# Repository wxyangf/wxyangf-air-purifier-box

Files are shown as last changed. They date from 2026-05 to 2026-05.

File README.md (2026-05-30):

Corsi-Rosenthol Inspired Air Purifier

Onshape Available Here: https://cad.onshape.com/documents/9fe4c8aaf9f949d23d7b46f2/w/0d3218e59a3f068a2d390f4a/e/8d3bb73142d813d5a04eb98a (This Is Based on the version tagged "Public Release")

The concept was to have a Corsi-Rosenthol like design, but a bit more refined.

The big problem that I aimed to address with this design is the difficulty of changing the filters in a regular Corsi-Rosenthol air purifier.

no flow rate tests, because it will heavily depend on the fans you decide to use.

TODO:

* write a proper bom
* add assembly instructions
* update the clip design to not self loosen if turned CCW
* add design for decorative side panels

images:

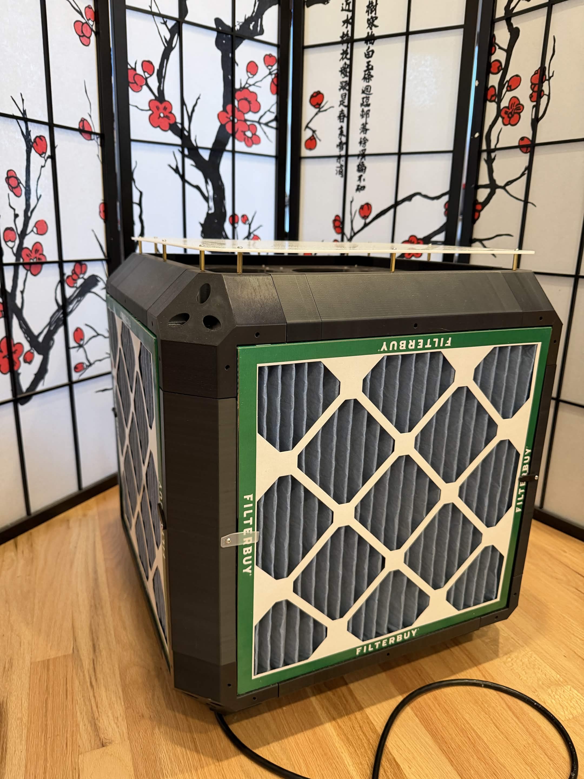
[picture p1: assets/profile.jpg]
image of air purifier in side profile

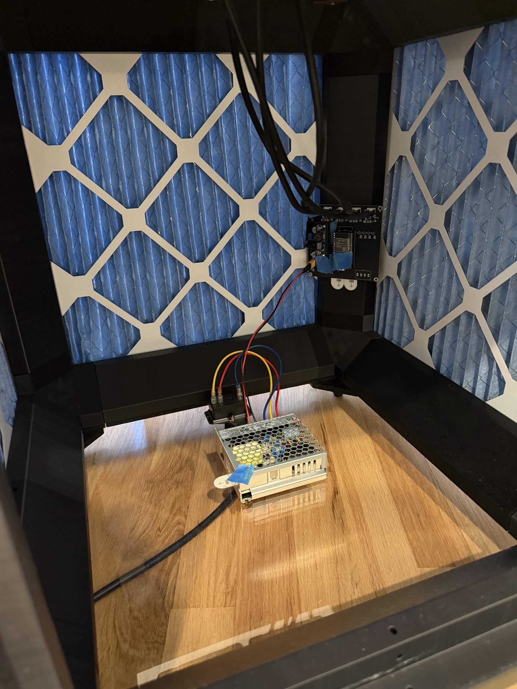
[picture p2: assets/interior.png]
image of the interior of the air purifier

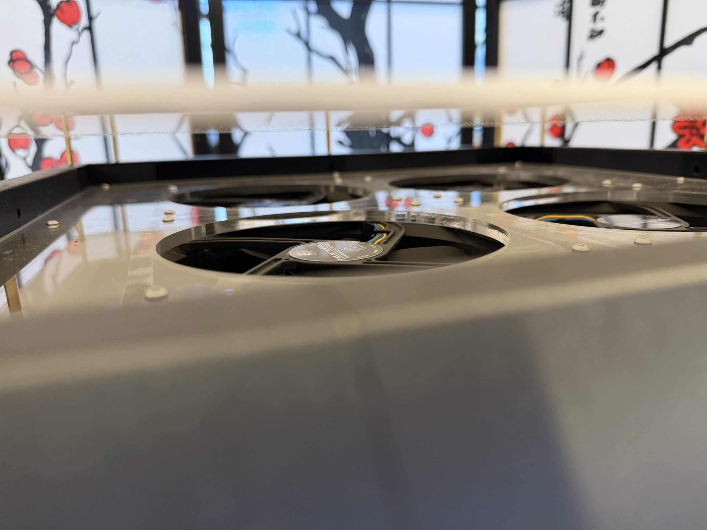
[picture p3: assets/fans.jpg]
image of the fans from the top, under the hat


Notes:

I was too lazy to design my own so voltage regulator part used: https://www.amazon.com/dp/B07VVXF7YX

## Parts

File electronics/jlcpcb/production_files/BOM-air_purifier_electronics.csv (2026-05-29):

Comment | Designator | Footprint | LCSC | Quantity
1.5k | R22 | R_0805_2012Metric_Pad1.20x1.40mm_HandSolder | C4310 | 1
100k | R10,R14,R3,R6 | R_0805_2012Metric_Pad1.20x1.40mm_HandSolder | C22356675 | 4
4.7k | R17,R18,R19,R20,R23 | R_0805_2012Metric_Pad1.20x1.40mm_HandSolder | C22356680 | 5
680 | R21 | R_0805_2012Metric_Pad1.20x1.40mm_HandSolder | C17798 | 1
BSS138 | Q1,Q2,Q3,Q4 | SOT-23 | C52895 | 4
Fan_4pin | M1,M2,M3,M4 | FanPinHeader_1x04_P2.54mm_Vertical | C19795120 | 4
LED | D1,D2,D3 | LED_0805_2012Metric_Pad1.15x1.40mm_HandSolder | C2296 | 3
TPS22810DBV | U3,U4,U5,U6 | SOT-23-6 | C205990 | 4
Conn_01x04_Socket | J2 | TerminalBlock_Altech_AK300-4_P5.00mm |  | 1
TestPoint_Probe | TP7 | TestPoint_THTPad_2.0x2.0mm_Drill1.0mm |  | 1
TestPoint_Probe | TP16 | TestPoint_THTPad_2.0x2.0mm_Drill1.0mm |  | 1
Conn_01x02_Socket | J1 | AMASS_XT30U-M_1x02_P5.0mm_Vertical |  | 1
TestPoint_Probe | TP14 | TestPoint_THTPad_2.0x2.0mm_Drill1.0mm |  | 1
TestPoint_Probe | TP18 | TestPoint_THTPad_2.0x2.0mm_Drill1.0mm |  | 1
TestPoint_Probe | TP3 | TestPoint_THTPad_2.0x2.0mm_Drill1.0mm |  | 1
TestPoint_Probe | TP17 | TestPoint_THTPad_2.0x2.0mm_Drill1.0mm |  | 1
TestPoint_Probe | TP9 | TestPoint_THTPad_2.0x2.0mm_Drill1.0mm |  | 1
TestPoint_Probe | TP15 | TestPoint_THTPad_2.0x2.0mm_Drill1.0mm |  | 1
TestPoint_Probe | TP4 | TestPoint_THTPad_2.0x2.0mm_Drill1.0mm |  | 1
TestPoint_Probe | TP10 | TestPoint_THTPad_2.0x2.0mm_Drill1.0mm |  | 1
TestPoint_Probe | TP11 | TestPoint_THTPad_2.0x2.0mm_Drill1.0mm |  | 1
TestPoint_Probe | TP13 | TestPoint_THTPad_2.0x2.0mm_Drill1.0mm |  | 1
1uF | C3 | C_0805_2012Metric_Pad1.18x1.45mm_HandSolder |  | 1
TestPoint_Probe | TP20 | TestPoint_THTPad_2.0x2.0mm_Drill1.0mm |  | 1
1uF | C2 | C_0805_2012Metric_Pad1.18x1.45mm_HandSolder |  | 1
1uF | C4 | C_0805_2012Metric_Pad1.18x1.45mm_HandSolder |  | 1
TestPoint_Probe | TP5 | TestPoint_THTPad_2.0x2.0mm_Drill1.0mm |  | 1
~ | U2 | buck_boost_module |  | 1
TestPoint_Probe | TP21 | TestPoint_THTPad_2.0x2.0mm_Drill1.0mm |  | 1
TestPoint_Probe | TP2 | TestPoint_THTPad_2.0x2.0mm_Drill1.0mm |  | 1
TestPoint_Probe | TP8 | TestPoint_THTPad_2.0x2.0mm_Drill1.0mm |  | 1
1uF | C1 | C_0805_2012Metric_Pad1.18x1.45mm_HandSolder |  | 1
TestPoint_Probe | TP19 | TestPoint_THTPad_2.0x2.0mm_Drill1.0mm |  | 1
TestPoint_Probe | TP12 | TestPoint_THTPad_2.0x2.0mm_Drill1.0mm |  | 1
TestPoint_Probe | TP6 | TestPoint_THTPad_2.0x2.0mm_Drill1.0mm |  | 1
ESP32-DevKitC | U1 | nodemcu-32s |  | 1
1uF | C9 | C_0805_2012Metric_Pad1.18x1.45mm_HandSolder |  | 1
100nF | C5 | C_0805_2012Metric_Pad1.18x1.45mm_HandSolder |  | 1
100nF | C6 | C_0805_2012Metric_Pad1.18x1.45mm_HandSolder |  | 1
1uF | C10 | C_0805_2012Metric_Pad1.18x1.45mm_HandSolder |  | 1
100nF | C8 | C_0805_2012Metric_Pad1.18x1.45mm_HandSolder |  | 1
100nF | C7 | C_0805_2012Metric_Pad1.18x1.45mm_HandSolder |  | 1
1uF | C11 | C_0805_2012Metric_Pad1.18x1.45mm_HandSolder |  | 1
1uF | C12 | C_0805_2012Metric_Pad1.18x1.45mm_HandSolder |  | 1

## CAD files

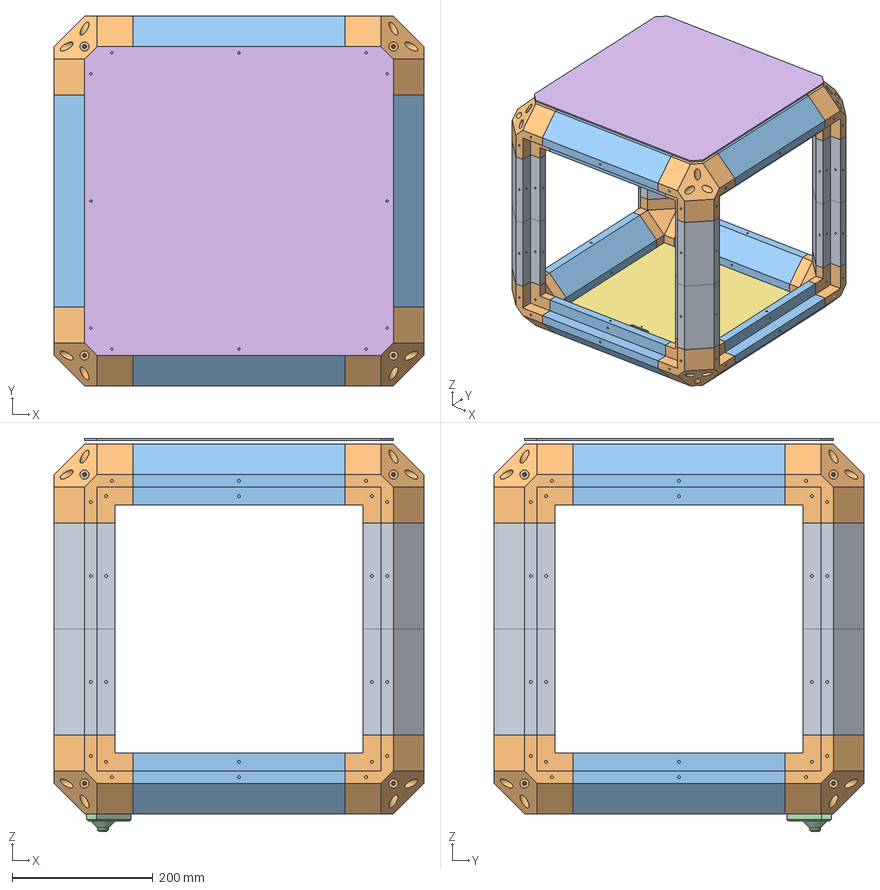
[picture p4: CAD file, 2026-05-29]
cad/frame_assembly_narrow.step
525.2 x 525.2 x 558.2 mm
beam_width x 8
corner x 8
beam_height x 8
foot
socket x 4
outside_panel
electronics_plate_part
fan_plate_part

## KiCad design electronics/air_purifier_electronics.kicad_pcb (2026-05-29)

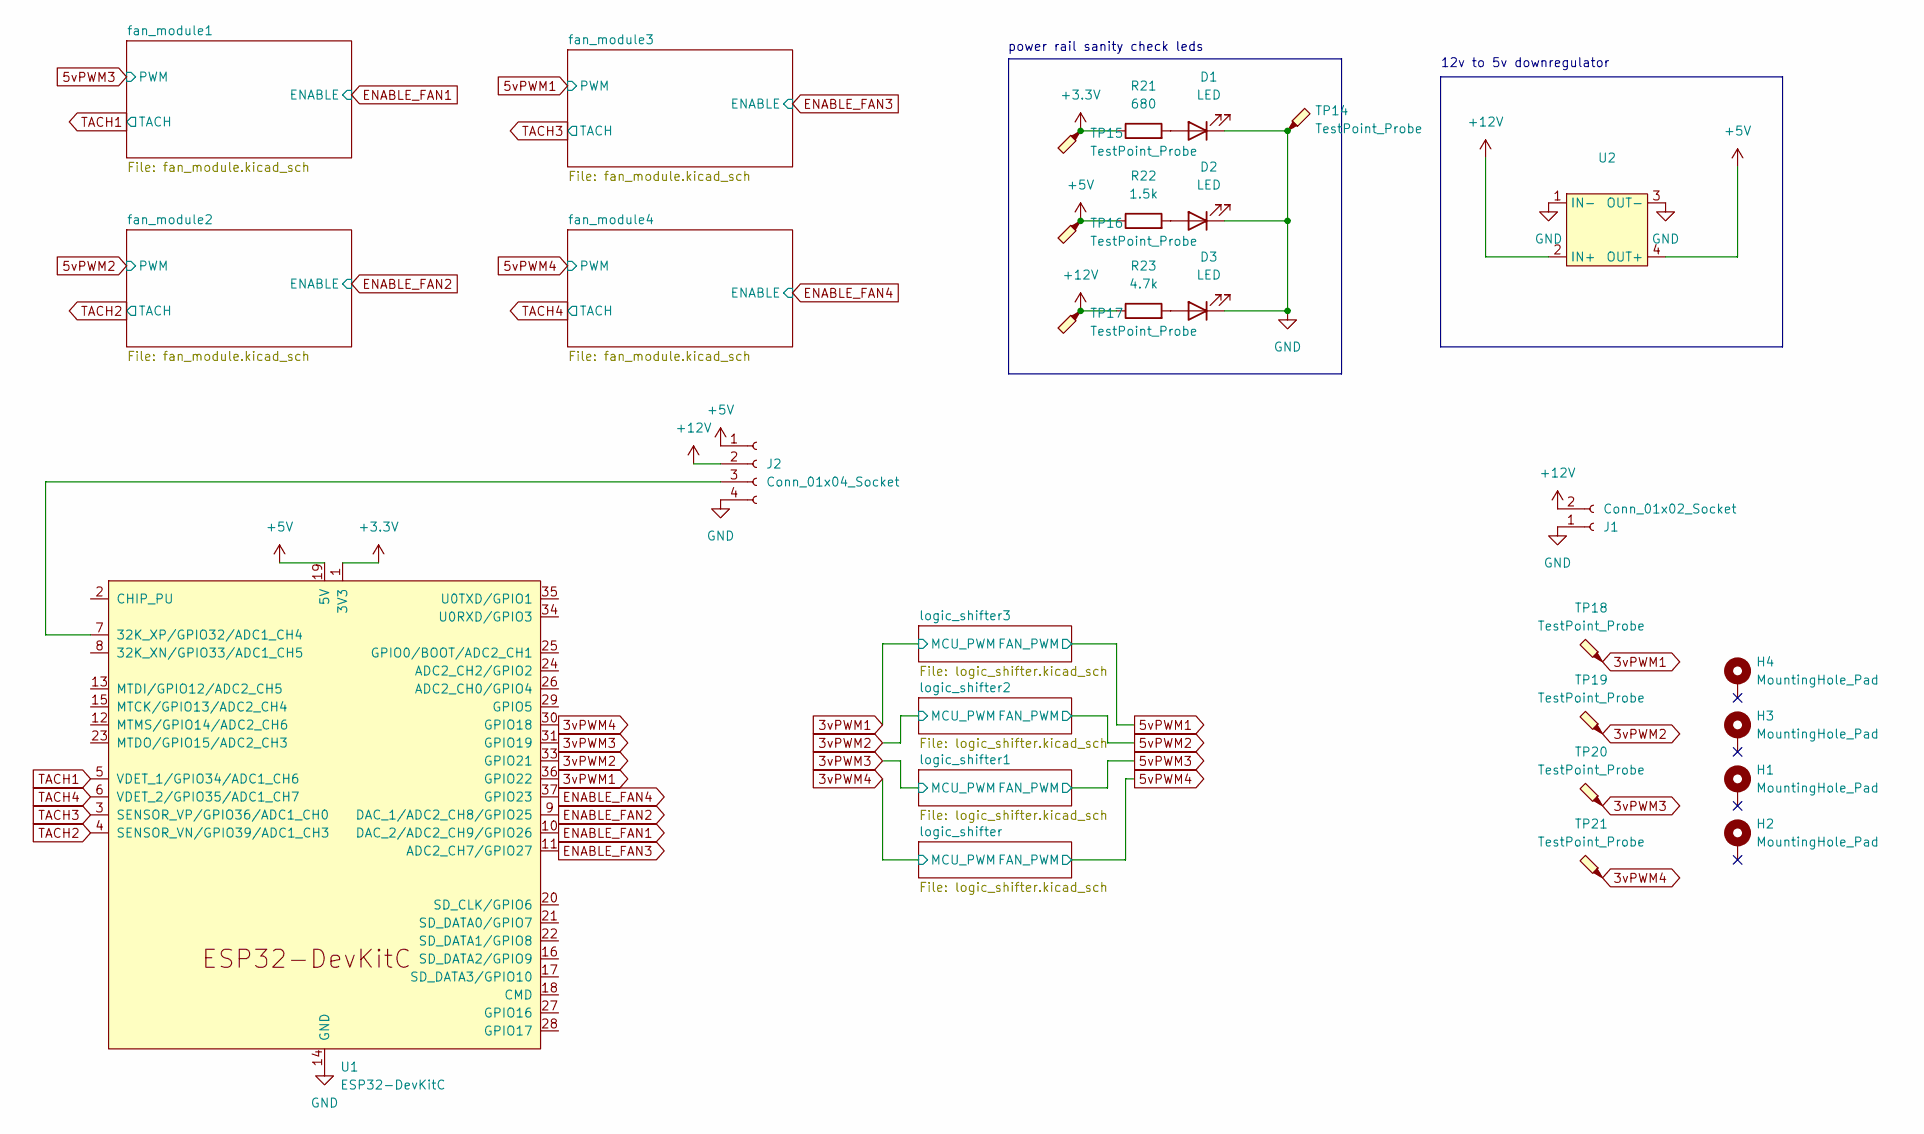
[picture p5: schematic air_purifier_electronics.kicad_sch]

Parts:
D1, D2, D3: LED; LED_0805_2012Metric_Pad1.15x1.40mm_HandSolder; LCSC C2296
H1, H2, H3, H4: MountingHole_Pad; MountingHole_3.2mm_M3_DIN965_Pad
J1: Conn_01x02_Socket; AMASS_XT30U-M_1x02_P5.0mm_Vertical
J2: Conn_01x04_Socket; TerminalBlock_Altech_AK300-4_P5.00mm
R21: 680; R_0805_2012Metric_Pad1.20x1.40mm_HandSolder; LCSC C17798
R22: 1.5k; R_0805_2012Metric_Pad1.20x1.40mm_HandSolder; LCSC C4310
R23: 4.7k; R_0805_2012Metric_Pad1.20x1.40mm_HandSolder; LCSC C22356680
TP14, TP15, TP16, TP17, TP18, TP19, TP20, TP21: TestPoint_Probe; TestPoint_THTPad_2.0x2.0mm_Drill1.0mm
U1: ESP32-DevKitC; nodemcu-32s
U2: buck_boost_module

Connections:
3vPWM1: TP18.1, U1.36 (GPIO22); also elsewhere on the board
3vPWM2: TP19.1, U1.33 (GPIO21); also elsewhere on the board
3vPWM3: TP20.1, U1.31 (GPIO19); also elsewhere on the board
3vPWM4: TP21.1, U1.30 (GPIO18); also elsewhere on the board
+3.3V: R21.1, TP15.1, U1.1 (3V3); also elsewhere on the board
+5V: J2.1, R22.1, TP16.1, U1.19 (5V), U2.4 (OUT+)
+12V: J1.2, J2.2, R23.1, TP17.1, U2.2 (IN+); also elsewhere on the board
ENABLE_FAN1: U1.10 (DAC_2/ADC2_CH9/GPIO26); also elsewhere on the board
ENABLE_FAN2: U1.9 (DAC_1/ADC2_CH8/GPIO25); also elsewhere on the board
ENABLE_FAN3: U1.11 (ADC2_CH7/GPIO27); also elsewhere on the board
ENABLE_FAN4: U1.37 (GPIO23); also elsewhere on the board
GND: D1.1 (K), D2.1 (K), D3.1 (K), J1.1, J2.4, TP14.1, U1.14 (GND), U1.32 (GND), U1.38 (GND), U2.1 (IN-), U2.3 (OUT-); also elsewhere on the board
unnamed: D1.2 (A), R21.2
unnamed: D2.2 (A), R22.2
unnamed: D3.2 (A), R23.2
unnamed: J2.3, U1.7 (32K_XP/GPIO32/ADC1_CH4)
TACH1: U1.5 (VDET_1/GPIO34/ADC1_CH6); also elsewhere on the board
TACH2: U1.4 (SENSOR_VN/GPIO39/ADC1_CH3); also elsewhere on the board
TACH3: U1.3 (SENSOR_VP/GPIO36/ADC1_CH0); also elsewhere on the board
TACH4: U1.6 (VDET_2/GPIO35/ADC1_CH7); also elsewhere on the board

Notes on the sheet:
12v to 5v downregulator
power rail sanity check leds

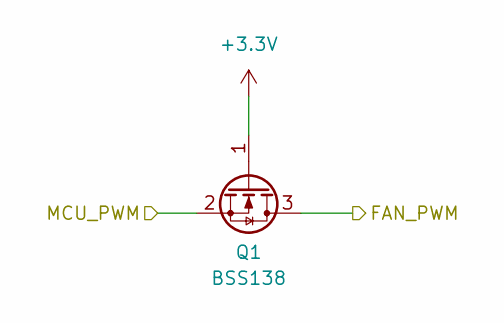
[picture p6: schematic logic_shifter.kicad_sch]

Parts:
Q1: BSS138; SOT-23

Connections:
3vPWM4: Q1.2 (S); also elsewhere on the board
5vPWM4: Q1.3 (D); also elsewhere on the board
+3.3V: Q1.1 (G); also elsewhere on the board

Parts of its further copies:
Q2, Q3, Q4: BSS138; SOT-23

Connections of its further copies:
3vPWM1: Q2.2 (S); also elsewhere on the board
3vPWM2: Q3.2 (S); also elsewhere on the board
3vPWM3: Q4.2 (S); also elsewhere on the board
5vPWM1: Q2.3 (D); also elsewhere on the board
5vPWM2: Q3.3 (D); also elsewhere on the board
5vPWM3: Q4.3 (D); also elsewhere on the board
+3.3V: Q2.1 (G), Q3.1 (G), Q4.1 (G); also elsewhere on the board

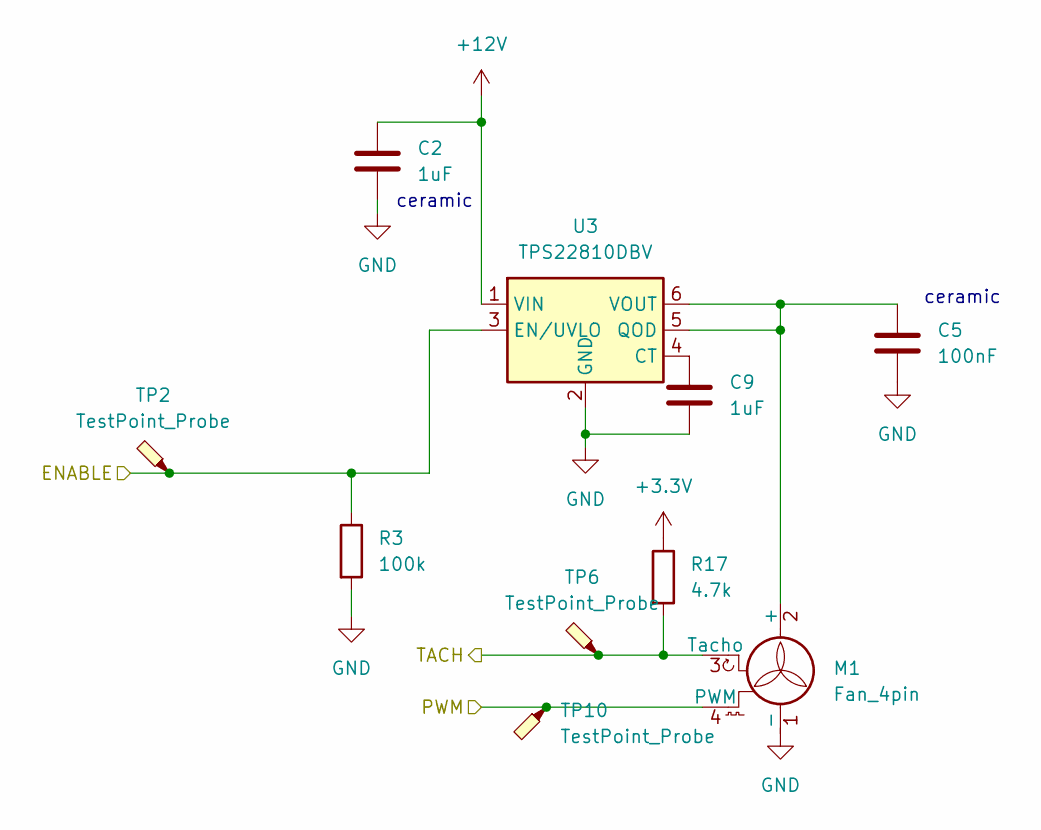
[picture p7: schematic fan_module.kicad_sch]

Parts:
C2, C9: 1uF; C_0805_2012Metric_Pad1.18x1.45mm_HandSolder
C5: 100nF; C_0805_2012Metric_Pad1.18x1.45mm_HandSolder
M1: Fan_4pin; FanPinHeader_1x04_P2.54mm_Vertical; LCSC C19795120
R3: 100k; R_0805_2012Metric_Pad1.20x1.40mm_HandSolder; LCSC C22356675
R17: 4.7k; R_0805_2012Metric_Pad1.20x1.40mm_HandSolder; LCSC C22356680
TP2, TP6, TP10: TestPoint_Probe; TestPoint_THTPad_2.0x2.0mm_Drill1.0mm
U3: TPS22810DBV; SOT-23-6

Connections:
5vPWM4: M1.4 (PWM), TP10.1; also elsewhere on the board
+3.3V: R17.1; also elsewhere on the board
+12V: C2.1, U3.1 (VIN); also elsewhere on the board
ENABLE_FAN4: R3.1, TP2.1, U3.3 (EN/UVLO); also elsewhere on the board
GND: C2.2, C5.2, C9.2, M1.1 (-), R3.2, U3.2 (GND); also elsewhere on the board
unnamed: C5.1, M1.2 (+), U3.5 (QOD), U3.6 (VOUT)
unnamed: C9.1, U3.4 (CT)
TACH4: M1.3 (Tacho), R17.2, TP6.1; also elsewhere on the board

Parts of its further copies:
C1, C3, C4, C10, C11, C12: 1uF; C_0805_2012Metric_Pad1.18x1.45mm_HandSolder
C6, C7, C8: 100nF; C_0805_2012Metric_Pad1.18x1.45mm_HandSolder
M2, M3, M4: Fan_4pin; FanPinHeader_1x04_P2.54mm_Vertical; LCSC C19795120
R6, R10, R14: 100k; R_0805_2012Metric_Pad1.20x1.40mm_HandSolder; LCSC C22356675
R18, R19, R20: 4.7k; R_0805_2012Metric_Pad1.20x1.40mm_HandSolder; LCSC C22356680
TP3, TP4, TP5, TP7, TP8, TP9, TP11, TP12, TP13: TestPoint_Probe; TestPoint_THTPad_2.0x2.0mm_Drill1.0mm
U4, U5, U6: TPS22810DBV; SOT-23-6

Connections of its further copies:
5vPWM1: M4.4 (PWM), TP13.1; also elsewhere on the board
5vPWM2: M3.4 (PWM), TP12.1; also elsewhere on the board
5vPWM3: M2.4 (PWM), TP11.1; also elsewhere on the board
+3.3V: R18.1, R19.1, R20.1; also elsewhere on the board
+12V: C1.1, C3.1, C4.1, U4.1 (VIN), U5.1 (VIN), U6.1 (VIN); also elsewhere on the board
ENABLE_FAN1: R6.1, TP3.1, U4.3 (EN/UVLO); also elsewhere on the board
ENABLE_FAN2: R10.1, TP4.1, U5.3 (EN/UVLO); also elsewhere on the board
ENABLE_FAN3: R14.1, TP5.1, U6.3 (EN/UVLO); also elsewhere on the board
GND: C1.2, C3.2, C4.2, C6.2, C7.2, C8.2, C10.2, C11.2, C12.2, M2.1 (-), M3.1 (-), M4.1 (-), R6.2, R10.2, R14.2, U4.2 (GND), U5.2 (GND), U6.2 (GND); also elsewhere on the board
unnamed: C6.1, M2.2 (+), U4.5 (QOD), U4.6 (VOUT)
unnamed: C7.1, M3.2 (+), U5.5 (QOD), U5.6 (VOUT)
unnamed: C8.1, M4.2 (+), U6.5 (QOD), U6.6 (VOUT)
unnamed: C10.1, U4.4 (CT)
unnamed: C11.1, U5.4 (CT)
unnamed: C12.1, U6.4 (CT)
TACH1: M2.3 (Tacho), R18.2, TP7.1; also elsewhere on the board
TACH2: M3.3 (Tacho), R19.2, TP8.1; also elsewhere on the board
TACH3: M4.3 (Tacho), R20.2, TP9.1; also elsewhere on the board

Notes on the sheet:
ceramic

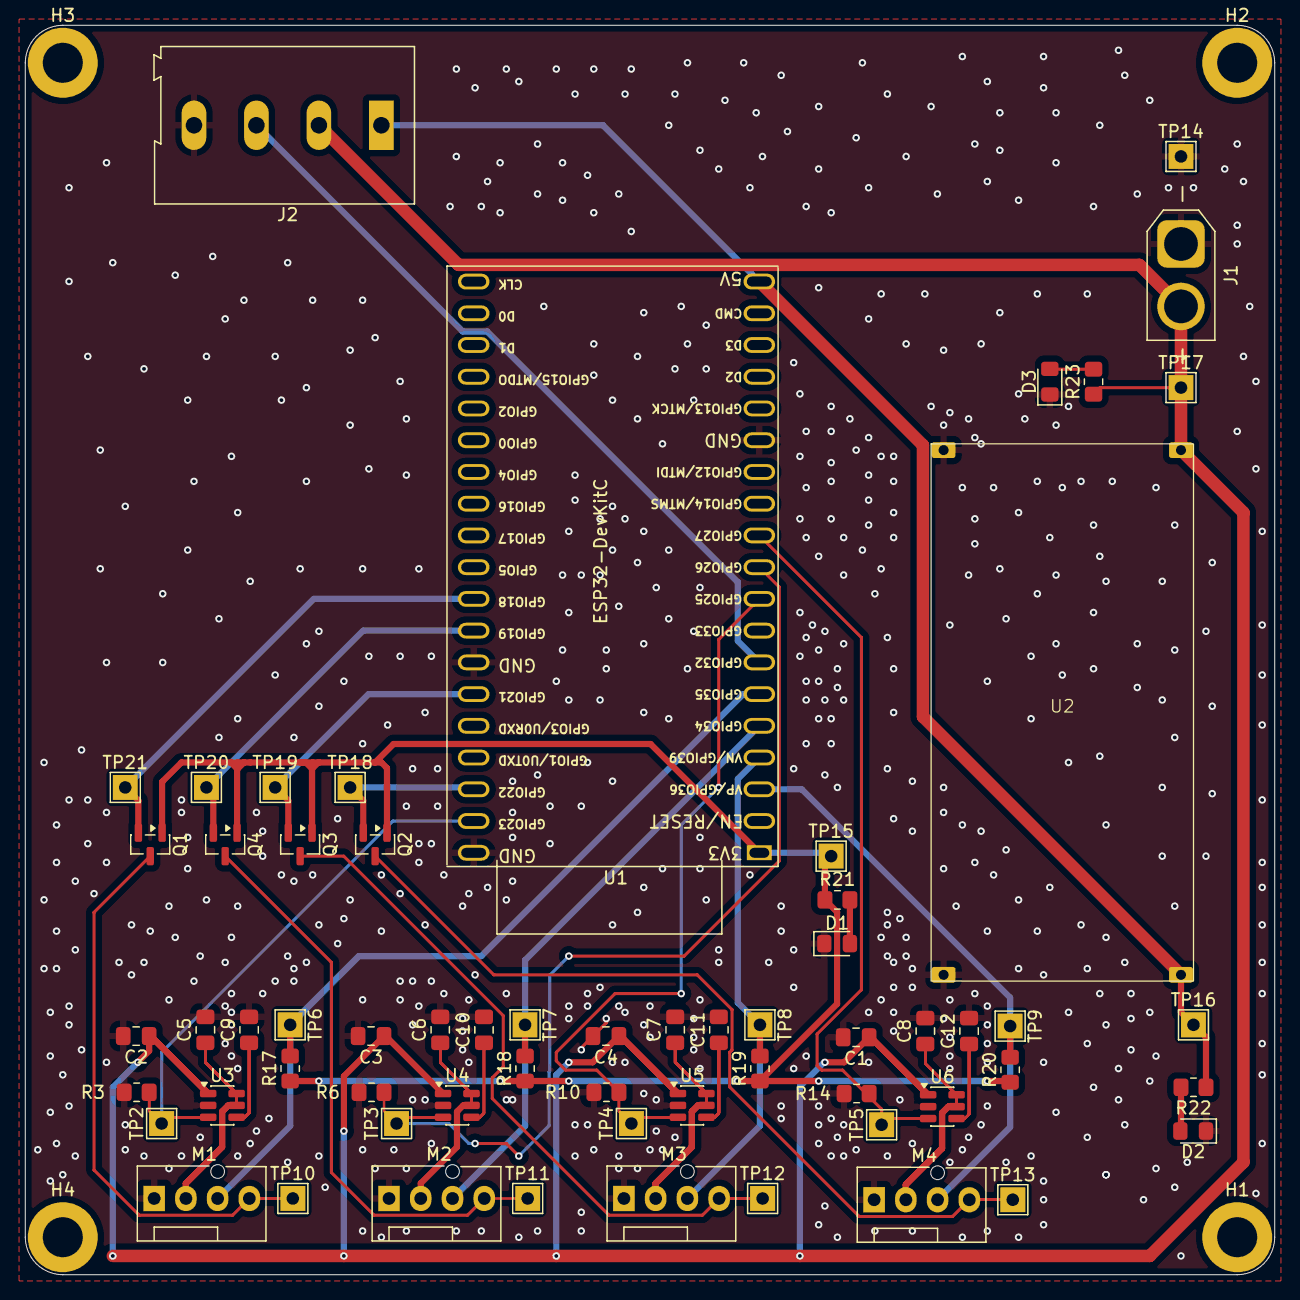
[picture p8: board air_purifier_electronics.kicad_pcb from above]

Board: 2 copper layers, 100.0 x 100.0 mm, 66 parts (0 on the bottom side), 32 nets.
